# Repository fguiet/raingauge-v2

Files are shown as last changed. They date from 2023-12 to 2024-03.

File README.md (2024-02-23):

# Raingauge v2

## The final project

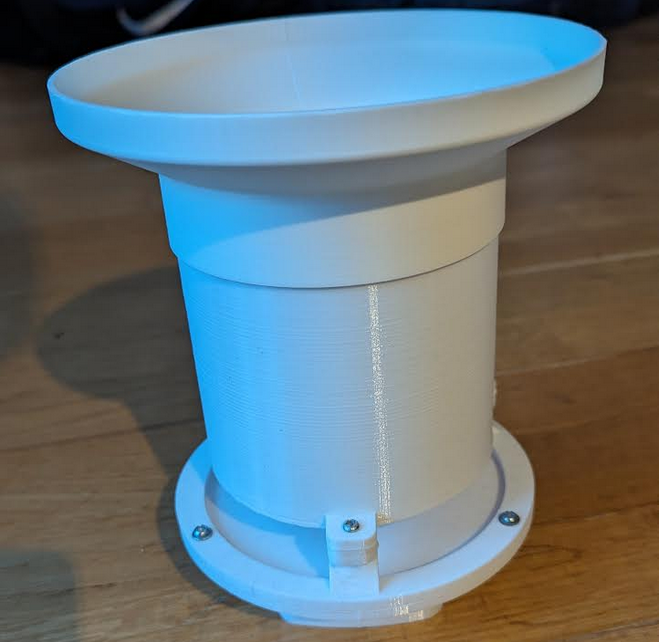
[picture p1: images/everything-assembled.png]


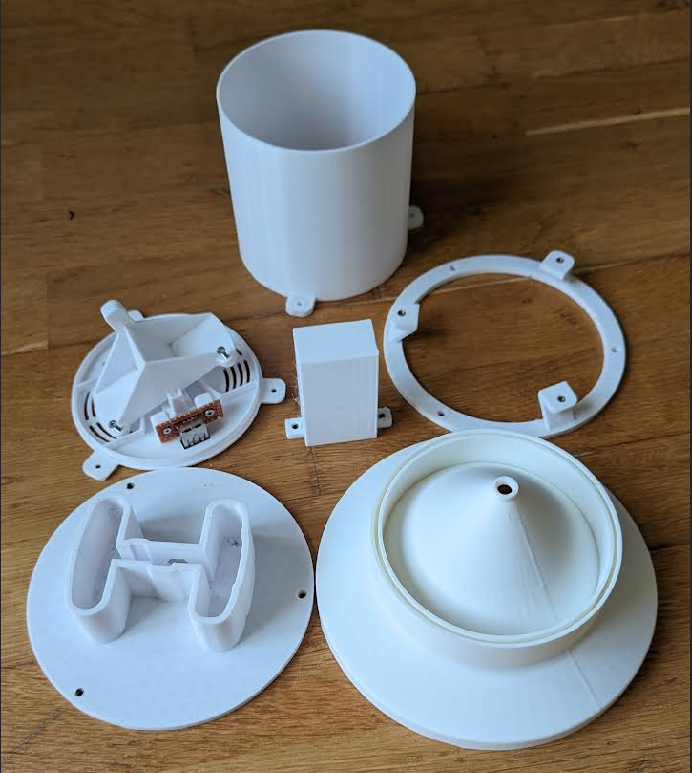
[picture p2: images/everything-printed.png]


This project is available on Thingiverse : <https://www.thingiverse.com/thing:6480016>

## PCB representation

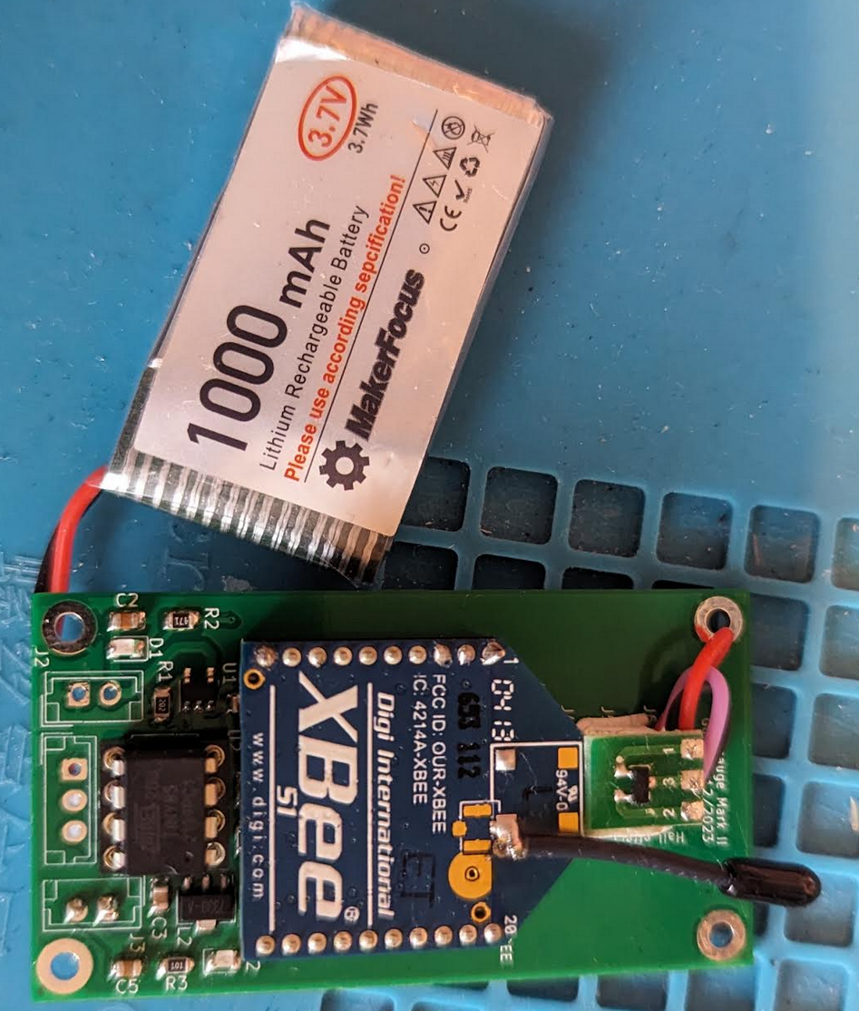
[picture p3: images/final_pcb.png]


## 3D representation

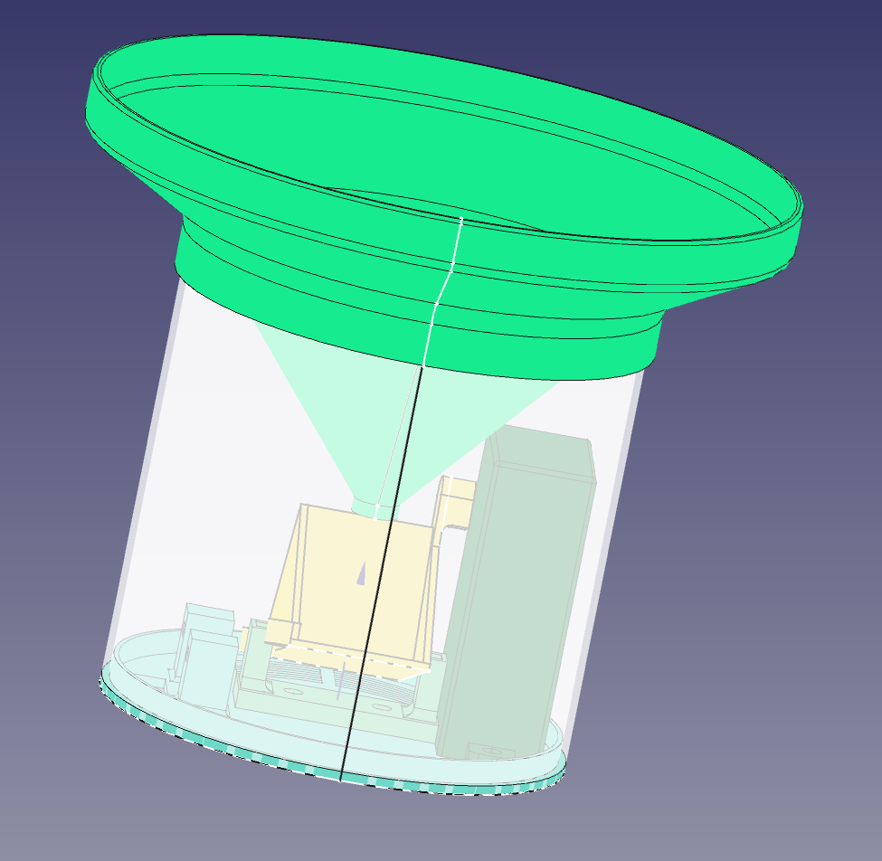
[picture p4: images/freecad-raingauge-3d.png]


## Compute how much water has fell ?

Funnel diameter = 15cm = 150 mm = 0.15m
Volume of each bucket (around) = 3ml = 0.0030l

Funnel area = pi*R² = 3.14 * 0.075² = 0,017669025 m2

X= 1/Aire * V = (1/0,017669025) * 0.0030 = 0.17 L par m2 (ou mm)

1mm = Une litre d'eau tombé sur une mètre carré

Résolution de mon pluvio = 0.17 L/m2 (c'est dans la norme)

## Programming the ATtiny85

Here is the ATtiny 85 pinout

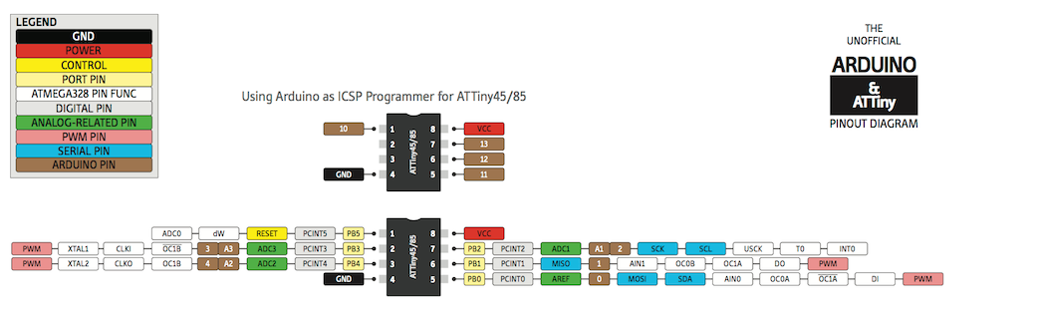
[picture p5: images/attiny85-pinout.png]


Using Arduino IDE v2, use this tutorial : <https://www.instructables.com/How-to-Program-an-Attiny85-From-an-Arduino-Uno/>

1. Use this following URL to add ATtiny Board to Arduino IE <https://raw.githubusercontent.com/damellis/attiny/ide-1.6.x-boards-manager/package_damellis_attiny_index.json>. File => Preferences => Aditional Board URL
2. Install the ATtiny boards (Board Manager on the menu on the left, then Install)
3. __Burn the ArduinoISP Exemple in the Arduino Board (select Arduino Board)__ => Don't forget that ! and make sure ATTiny pin are well connected to the bread board
4. Select ATtiny 85 board
5. Select Clock Internal 1 Mhz (it is ok for this project)
6. Select Programmer => Arduino as ISP
7. Burn Boatloader
8. Open sketch to upload then click on the menu Sketch => Upload using programmer

A quick overview of the Arduino and ATtiny 85 connexion.

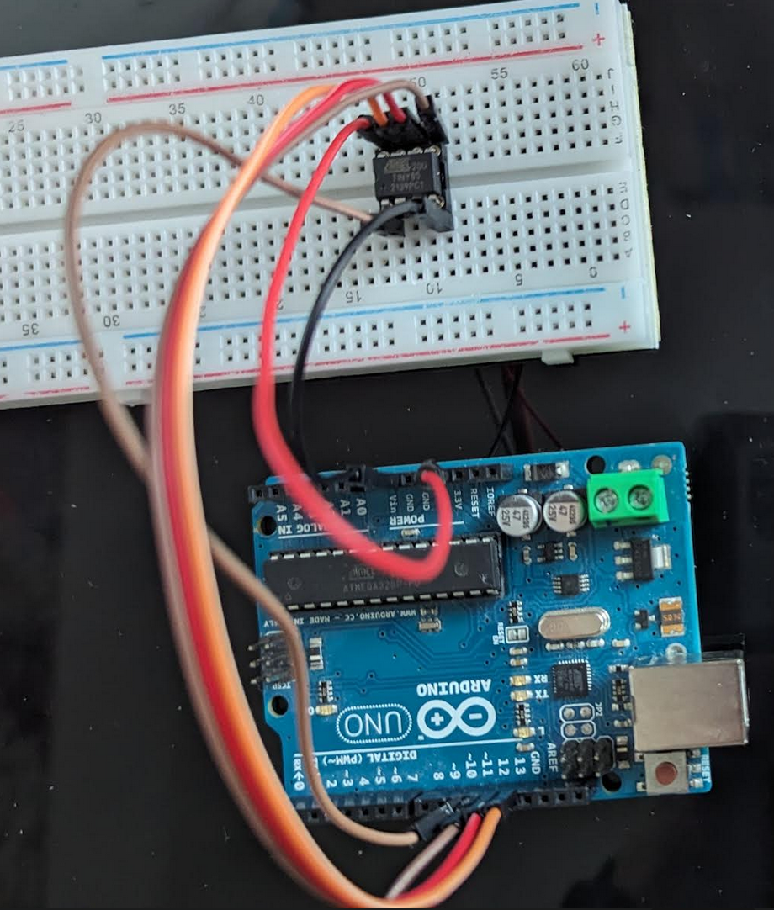
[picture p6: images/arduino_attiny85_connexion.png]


__To program (Arduino <=> ATtiny 85):__

VCC (3.3v ou 5V) <=> VCC (ATtiny pin8)
Arduino GND <=> GND (ATtiny pin4)
Arduino Pin 10 <=> ATtiny Pin1
Arduino Pin 11 <=> ATtiny Pin5
Arduino Pin 12 <=> ATTiny Pin6
Arduino Pin 13 <=> ATTiny Pin7

## Interrupt and power saving stuff with ATtiny 85

See <https://forum.arduino.cc/t/attiny84-sleep-issues/199824/8>
See <http://www.gammon.com.au/power>
See <https://www.marcelpost.com/wiki/index.php/ATtiny84_ADC>

Extract from ATtiny datasheet p49.

²> 9.2 External Interrupts
> Note that recognition of falling or rising edge interrupts on INT0 requires the presence of an
> I/O clock, as described in “Clock Sources” on page 25.

## How to debug using Serial Adapter 

Careful use 3.3v on your serial adapter.

Connect this way:

USB To Serial Adapter <-> ATTiny
GND <-> GND
RX <-> Pin 7 (PB2) 

Then, power the circuit by an external alimentation at 3.3v (no need to power the USB Serial Adapter to VCC pin)

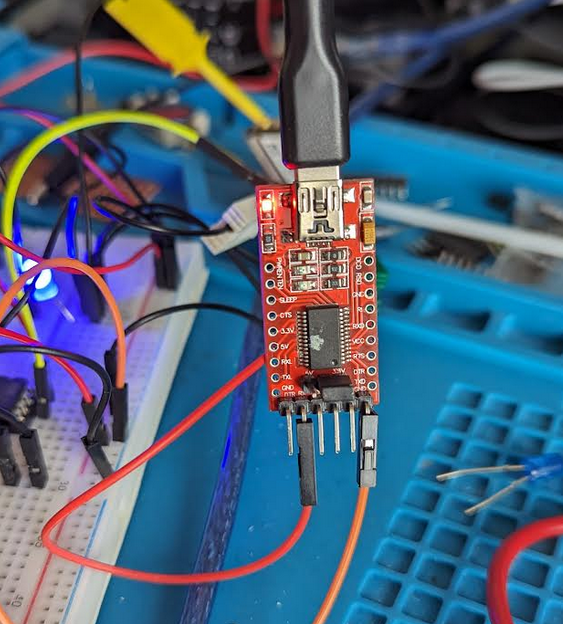
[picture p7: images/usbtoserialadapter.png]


## Power consumption

Using the PPK II (Nordic Power Profiler Kit II), the device consume about 13uA when sleeping and 60mA when sending data.

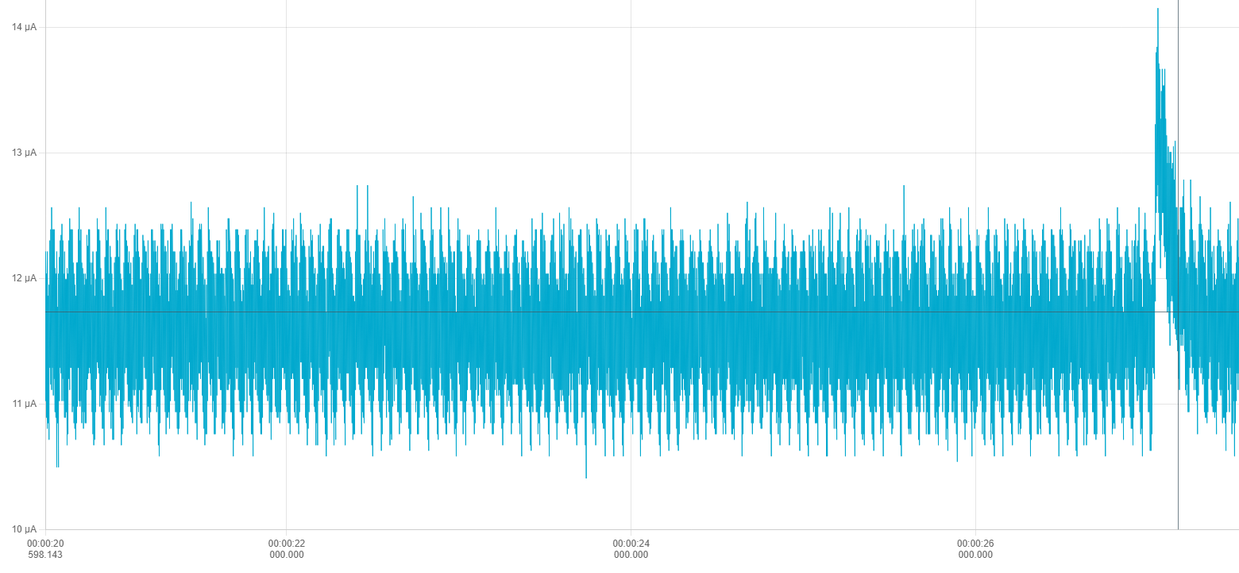
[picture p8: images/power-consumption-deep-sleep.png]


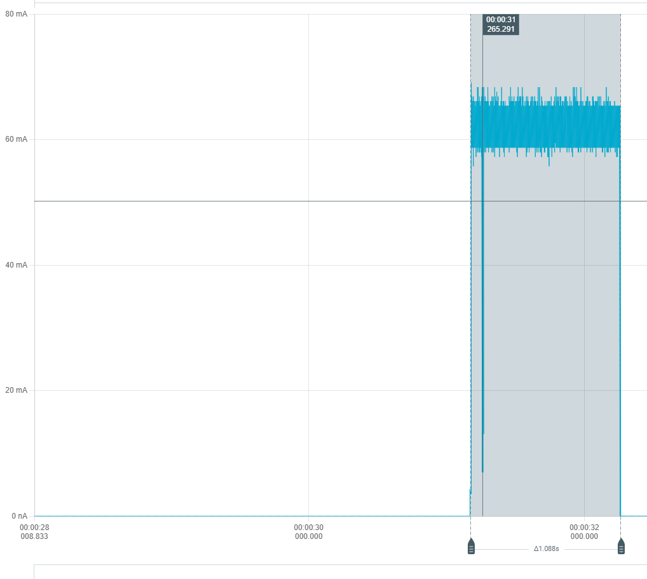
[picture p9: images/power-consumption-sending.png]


VOUT of the PPK II should be connected to VIN of the device and GND to GND.

See [Get your Power Profiler Kit II up and running](https://www.youtube.com/watch?v=B42lPvkUSoc)

## Configuring XBee S1 with XCTU v6.5.13

I am using old XBee S1.

At the begining of the project I was using the transparent mode (AT).

But I changed to API Mode as it offers more options (like the RSSI)

### XBee firmware update

Update the XBee firmware with last version using XCTU v6.5.13

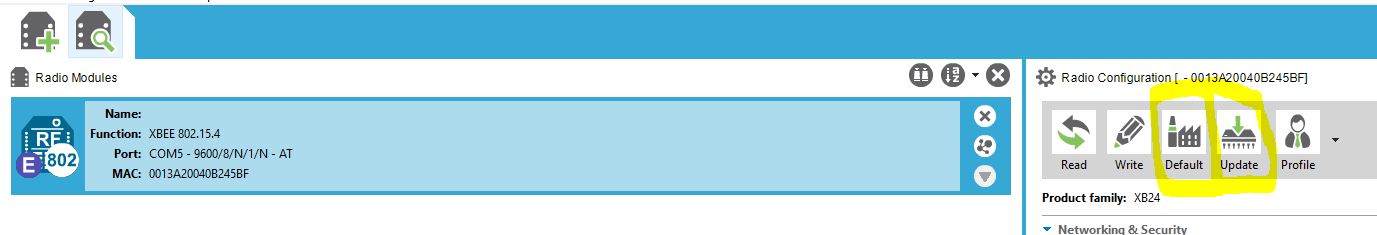
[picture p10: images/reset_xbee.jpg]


Click on Default (To reset XBee to factory default), then Write
Click on Update to upload the last firmware available for this XBee S1 unit

In my case as of 2023/12 :



To make the Xbee talks to each other just config them with the same Channel and PAN (Personnal Area Network ID). Messages will be broadcasted.



### Test XBee communication (deprecated as it shows transparent mode)

You can use XCTU to test that a mesage is correcly sent.

In my case I have got an Raspberry Pi with NodeRed installed and an XBeee connected to the Raspberry Pi.

Just use the XCTU Console and send a test packet, here : "Rainguage projet rocks!" in a JSON format

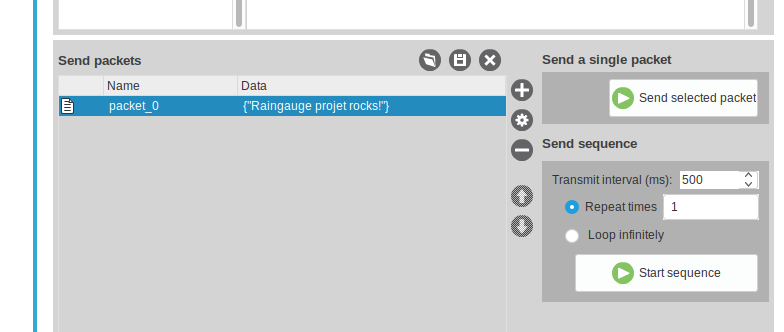
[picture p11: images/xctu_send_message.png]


Here a part of the NodeRed flow I am using.

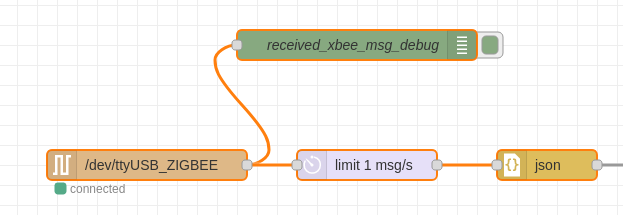
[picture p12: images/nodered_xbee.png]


Careful, you must configure the NodeRed serial flow to split a message as soon as the '}' character is reveiced (end of JSON message)

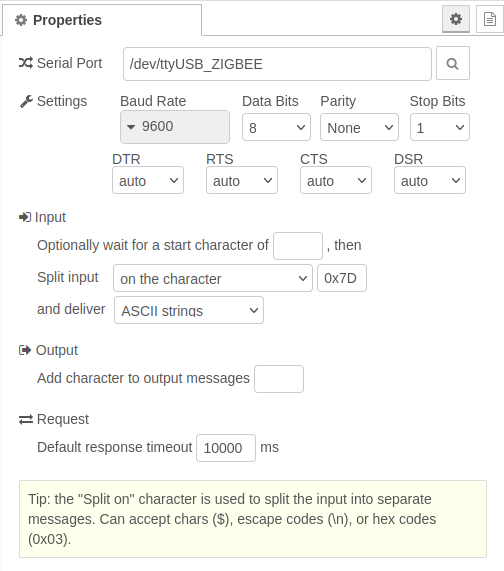
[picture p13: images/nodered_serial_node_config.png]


If everything is going well then you should received the message on the NodeRed debug console

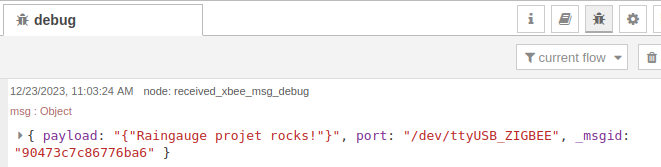
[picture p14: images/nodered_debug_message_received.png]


### XBee pinout

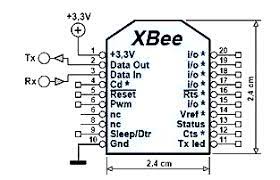
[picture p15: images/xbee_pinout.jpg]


### Sleep mode

To config the Xee to use the sleep mode, just change the sleep mode setting



Sleep mode will be control by pin 9, see <https://www.digi.com/resources/documentation/Digidocs/90001456-13/reference/r_wk_sleep_mode.htm>

PIN 9 HIGH : Xbee sleeps
PIN 9 DOWN : Xbee awake

### XBee speed communication

Don't forget to set Xbee serial speed communication to 38400 bauds as the ATtinySerialOut library use this speed.

### New way of communicating : Using the API Mode

I was using Transparent Mode before (AT) but there is another mode called API Mode that offers more options and controls

See [API mode in detail](https://www.digi.com/resources/documentation/Digidocs/90001942-13/concepts/c_api_mode_detailed.htm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)

See [API Mode 2 frame Structure](https://www.digi.com/resources/documentation/Digidocs/90001942-13/concepts/c_api_frame_structure.htm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)C

Supported frames are listed here : <https://www.digi.com/resources/documentation/Digidocs/90001942-13/reference/r_supported_frames_zigbee.htm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>

I am using the 64-bit Transmit Request - 0x00 frame. I know that I should use the 0x10 frame tpye but I am using old XBee S1 and they only support 802.15.4 protocol stack.

See [64-bit Transmit Request - 0x00](https://www.digi.com/resources/documentation/Digidocs/90001477/reference/r_frame_0x00.htm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)

In API Mode 2, some characters need to be escaped:

See : <https://stackoverflow.com/questions/55861574/difference-between-api-1-and-api-2-mode-of-xbee>

* 0x7E (Start of frame) => 0x7D 0x5E (escaped)
* 0x7D (start of escape sequence) => 0x7D 0x5D (escaped)
* 0x13 (XOFF) => 0x7D 0x33 (escaped)
* 0x11 (XON) =>	0x7D 0x31 (escaped)

In API 2 mode, the length field does not include any escape character in the frame and the checksum is calculated with non-escaped data.

All bytes except for the start delimiter must be escaped if needed.

* End Device XBee configuration

Here is what I changed in the XBee configuration with XCTU

CH - Channel = C
ID - PAN ID = 666
SM - Sleep mode = Pin Hibernate [1]
BD - Interface Data Rate = 38400 [5]
AP - API Enable = API Enabled w/PPP [2]

* Coordinator XBee configuration

CH - Channel = C
ID - PAN ID = 666
CE - Coordinator Enable = Coordinator [1]
BD - Interface Data Rate = 38400 [5]
AP - API Enable = API Enabled w/PPP [2]
RR - XBee Retries = 3 (because the RSSI was not good I tried this setting)

## Librairies used in this project

* ATTinySerialOut

To communicate with the XBee (send data), this project used the following library : `ATtinySerialOut`, version 2.2.0 (2023/12)

GitHub : <https://github.com/ArminJo/ATtinySerialOut/>

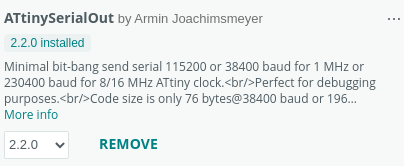
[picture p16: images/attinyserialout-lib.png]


* LowPower

This project is using this library <https://github.com/ortegafernando/Low-Power> to allow the ATTiny 85 power management

__Note__

To use an external library for a Arduino IDE Project, just copy the library source in the librairies folder of Arduino IDE

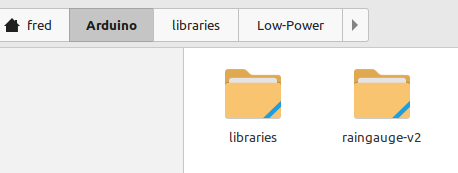
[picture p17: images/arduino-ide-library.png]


## Freecad

__Some notes__

* On ne peut pas utiliser le mirroring sur la pièce que l'on veut "mirrorer" n'a pas de lien avec un objet du body en cours (pas de corps multiples dans un body)

* Utilisation de ShapeBinder pour pouvoir avoir des points de repères d'un autre body (voir vidéo : <https://www.youtube.com/watch?v=KYD9Ojugi8Q>)

### Support tipping bucket

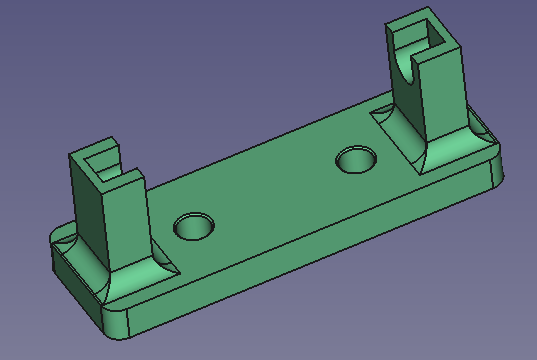
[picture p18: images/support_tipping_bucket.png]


Les trous pour placer les inserts font 4.2mm sur Freecad. les inserts à utiliser sont des M3*4 (4 mm de haut pour type vis M3)

## Pull up / pull down

Quick reminder about pullup/pulldown : <https://arduino.developpez.com/cahiers-pratiques/resistance-pullup-pulldown/>

## Kicad

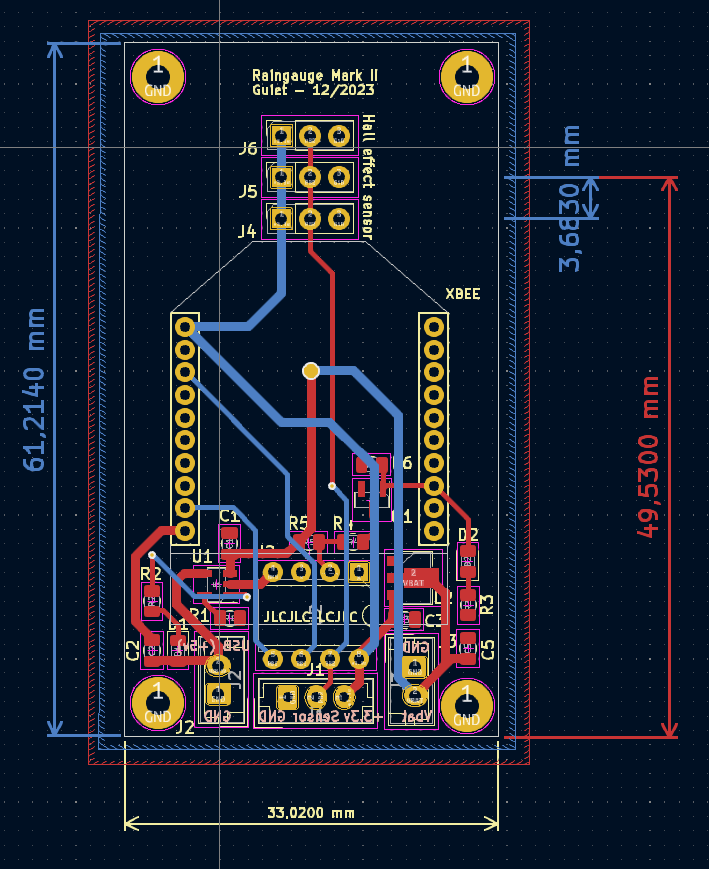
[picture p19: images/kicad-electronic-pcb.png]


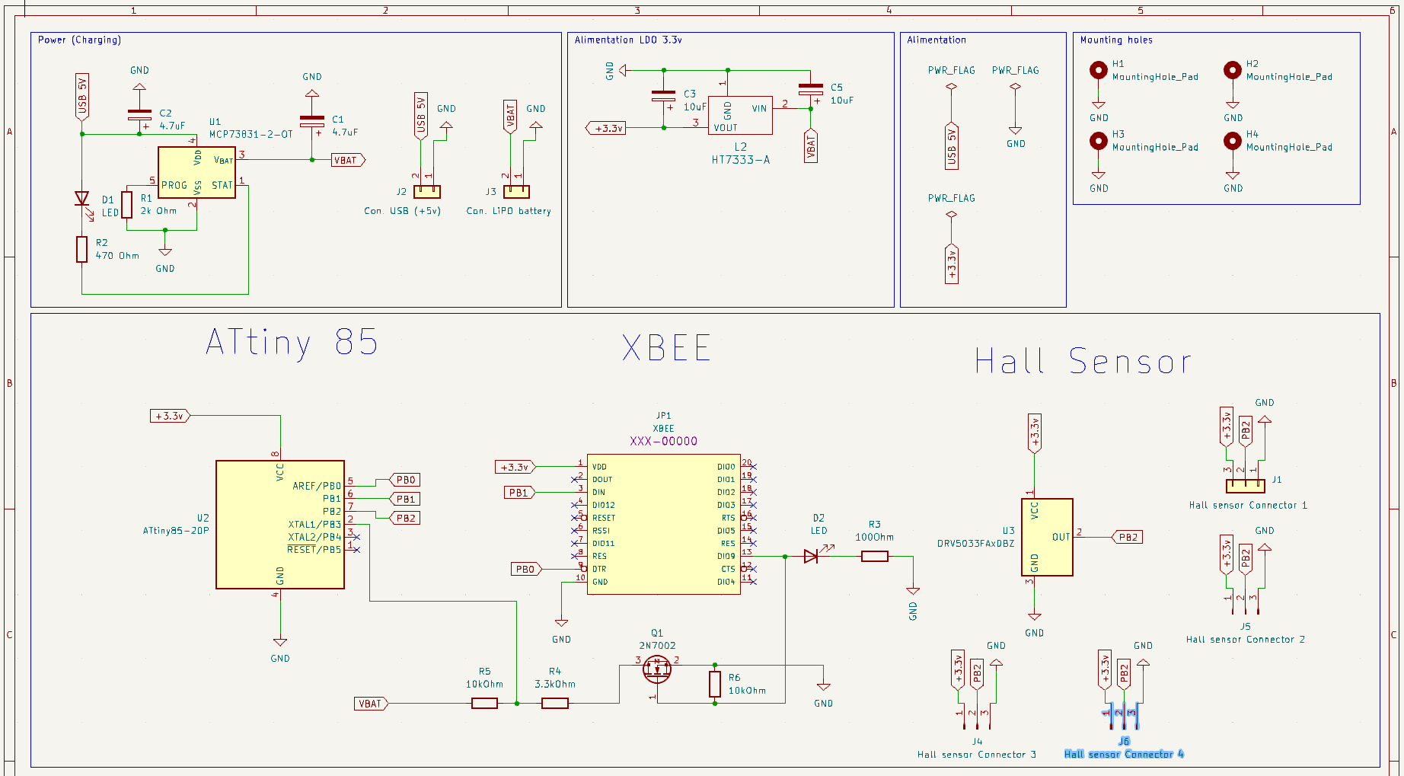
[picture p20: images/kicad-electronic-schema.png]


Ce tuto : <https://www.youtube.com/watch?v=RpVIrzEUsIM> ou <https://www.youtube.com/watch?v=dAck3bxzehA> ou <https://www.youtube.com/watch?v=nYybg5KdaT8>

__Note__ :

Suppression du snap sur le PCB Editor afin de placer les composants à un endroits précis : utiliser la touche CTRL

__Grandes étapes__

1. Editeur de schéma électronique, remplir le cartouche pour définir les informations du PCB

Fichier, Ajustage page

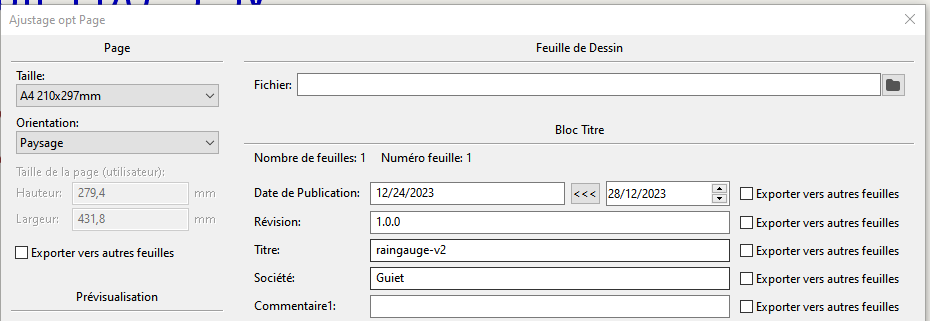
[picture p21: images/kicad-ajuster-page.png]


2. Place all your components

Shortcut

M : Move
R : Rotate
Tab  : Pour bouger le composant avec les fils accrochés

Pour vérifier que le circuit est ok on peut cliquer sur le bouton : 



__Note__

* Essayer de mettre par convention VCC en haut et GND en bas au niveau du positionnement
* Il existe des labels global et local (A voir sur le net la différence)
* Possibilité de créer des feuilles hiérarchiques (si jamais on a un schéma très grand alors on peut le splitter, après y'a les notions de labels hiérarchiques, global, etc etc...)
* Il faut bien penser à définir les pins qui alimentent le schéma électrique (= PWR_FLAG)

3. Annotation de la schématique (pour numéroter les composants)

Normalement avec Kicad 7, les éléments sont numérotés automatiquement.
Sinon, cliquer sur le bouton: 



4. Assigner les empreintes des composants de la schématique



5. Génération de la net liste

Inutile dans Kicad 7 ?

6. Editeur de circuit imprimé et lecture de la net liste

Inutile dans Kicad 7 ?

7. Placement des composants sur l'éditeur de PBB

On passe sur cet écran en cliquant sur :



Récupération des contraintes JLCPCB : <https://github.com/sethhillbrand/kicad_templates/tree/master/JLCPCB_1-2Layer> prendre le fichier JLCPCB.pro

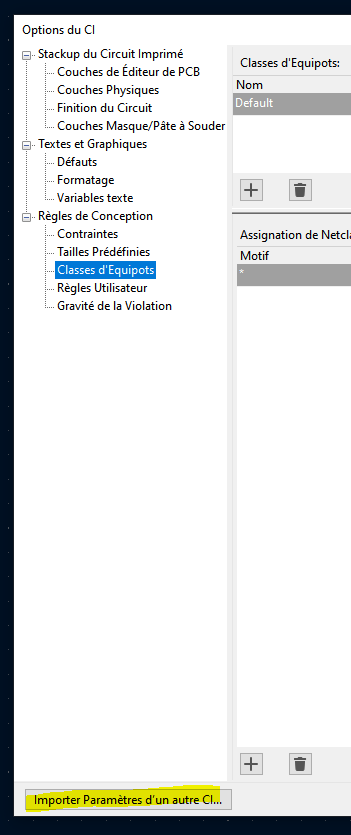
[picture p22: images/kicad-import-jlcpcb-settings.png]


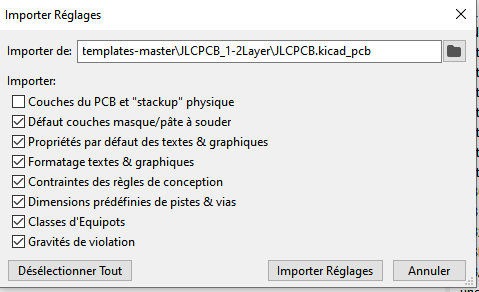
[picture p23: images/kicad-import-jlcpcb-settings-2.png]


Fichier, Ajustage page pour personnaliser le cartouche comme pour l'éditeur de schéma électronique

Pour gérer la largeur des pistes en fonction du type de piste (VCC) : Fichiers, Options CI, Classe d'Equipots, j'utilise 0.4mm pour les pistes classiques et 0.8mm en VCC

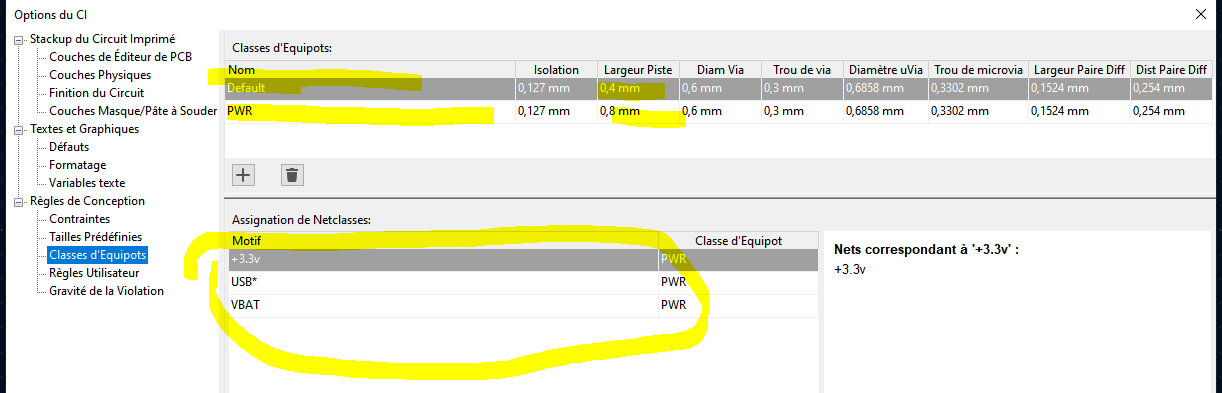
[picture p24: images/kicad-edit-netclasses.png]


Penser à modifier la valeur par défault de la largeur des pistes à 0.4mm

Short Cut

v: change layer (front / bottom)

__Notes__

Layers intéressantes 

F. Silks pour écrire sur le front Silk Screen
B. Silks pour écrire sur le bottom Silk Screen
Dwgs.User pour faire des dessins
F. Courtyard : place que prend le composant front
B. Courtyard : place que prend le composant bottom (on peut afficher ou pas)

Quand il y a beaucoup d'éléments sur le PCB, on peut utiliser le filtre de sélection afin de limiter la sélection à l'objet que l'on désire (exemple j'avais besoin de bouger les références des composants sur la layer silkscreen)

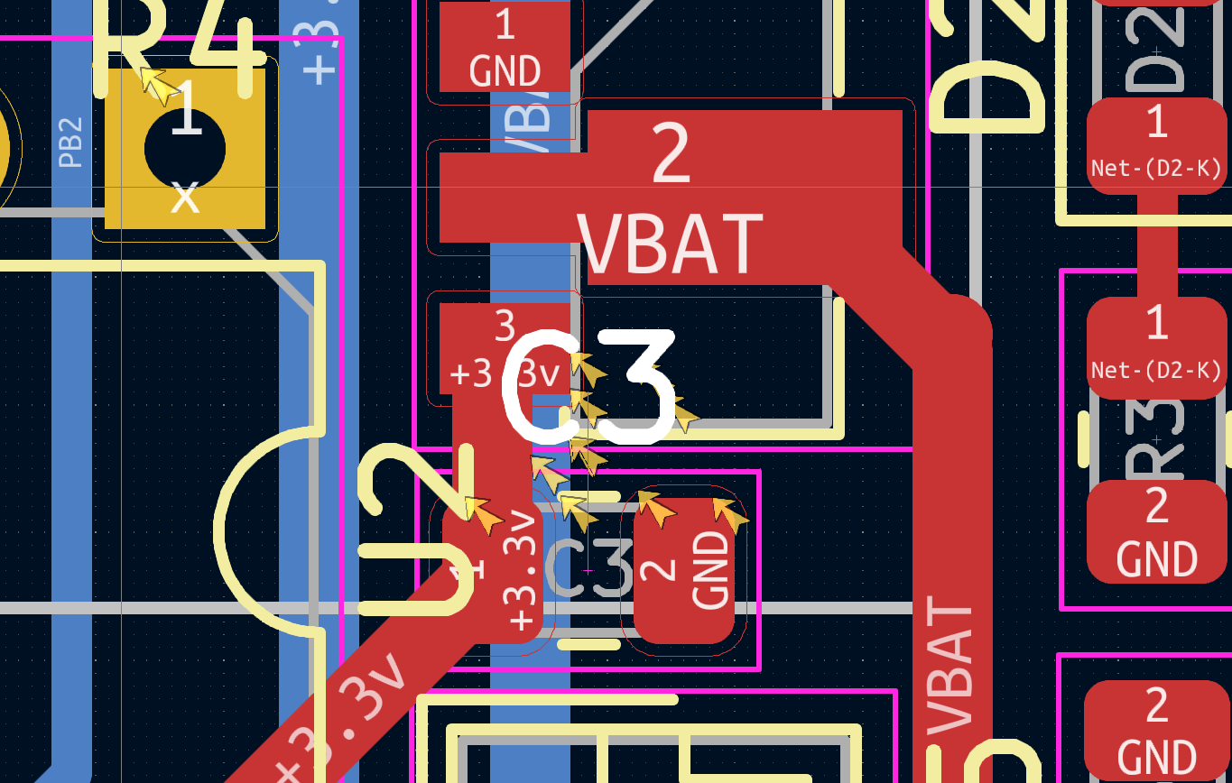
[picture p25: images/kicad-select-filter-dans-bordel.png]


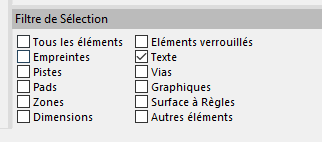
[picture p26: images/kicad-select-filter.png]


8. Couche Edge cut (contour de carte)

On trace autour des composants pour couper le PCB à la taille désirée

9. Routage

Pour la largeur, bien penser à sélectionner utiliser largeur de netclasse.
Attention, dans netclasse il faut avoir penser à modifier la valeur par défaut pour la largeur des pistes à 0.4mm et mettre 0.8mm pour les pistes de puissance (PWR)



Voici ce qu'il faut respecter lors que l'on trace des routages pour éviter les pbs d'électromagnétisme.

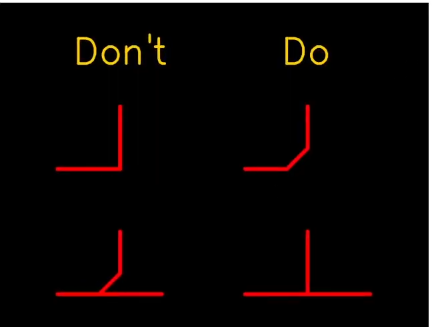
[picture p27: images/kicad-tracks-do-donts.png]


Quand on a des tracks qui se croisent sur la couche du dessus et dessous il faut qu'elles soient perpendiculaires:

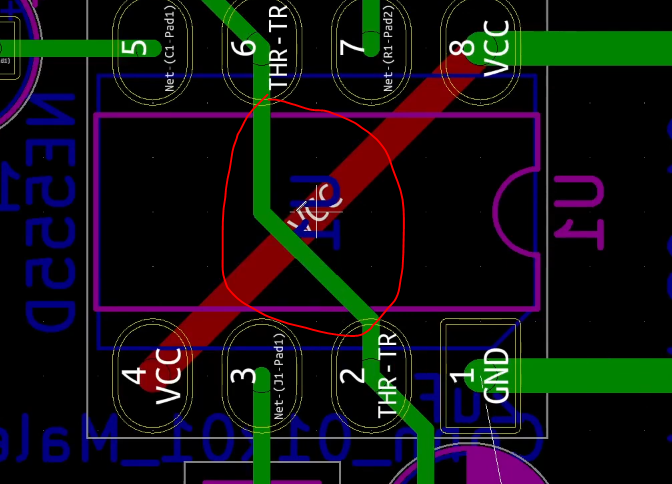
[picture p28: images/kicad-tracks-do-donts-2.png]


Couche F. Cu (Front en rouge couche du dessus)
Couche B. Cu (Front en vert couche du dessous)

Ne pas relier les GND, ca sera automatique avec le plan de masse

__Notes__

Short cut

D : Pour modifer les tracks sans tous casser
I : Au dessus d'une track permet de sélectionner toute la track

10. Ajouter la zone ground (sur layer front / bottom)

Utiliser l'outil : 



10. Serigrafie avec couche Drawing User pour mettre les indications + - et autres ou layer F. Silks et B. Silks

11. Générer les fichiers Gerber, Fichier Tracer (ne pas oublier de générer le fichier de percage)

Mettre un texte JLCJLCJLCJLC sous un composant (layersilk screen)

D'abord générer le fichier de percage (generate drill file) et ensuite plot avec les options par défaut.

12. Faire un Zip et envoyer sur JLCPCB par exemple

## References

* snapeda pour récupérer des composants kicad : <https://www.snapeda.com/>

* Madman's Github : <https://github.com/PricelessToolkit/MailBoxGuard>

* ATTiny and LoRa : <https://github.com/novag/LoRa-ATtiny-Node>

* MrDIY : <https://gitlab.com/MrDIYca/ultra-low-power-trigger-sensors-version-3>

* [MakerMeik : ESP8266 as Window Sensor with years of battery life](https://www.youtube.com/watch?v=vxbuO1zWo3w)

* [ESP32-C3 based Smart Door/Window sensor | DEEP SLEEP 30nA? | Long battery life 5/10 years](https://www.youtube.com/watch?v=he_Z-mDLnlM)

* [Raingauge version 1](https://www.youtube.com/watch?v=DnNW4rJkFhY&t=649s)

* [Raingauge version 2](https://www.youtube.com/watch?v=P2-hs2m6eCE)

* [Communication XBee](https://www.redohm.fr/2015/03/communication-xbee/)

* [Configuration XBee](https://www.electro-info.ovh/configuration-d-un-module-XBEE-avec-XCTU)

* [Un programme qui ressemble a ce que je fais](https://github.com/cano64/ATTiny85-ATTiny84-BMP085-Arduino-Library-FastAltitude/issues/1)

* [How works a switch without neutral](https://www.youtube.com/watch?v=VNYcD7MEp4A)

* [Inspiring sketch : OpenWindowAlarm](https://github.com/ArminJo/ATtinySerialOut/blob/master/examples/OpenWindowAlarm/OpenWindowAlarm.ino)

* [OpenWindowAlarm documentation](https://github.com/ArminJo/Arduino-OpenWindowAlarm)

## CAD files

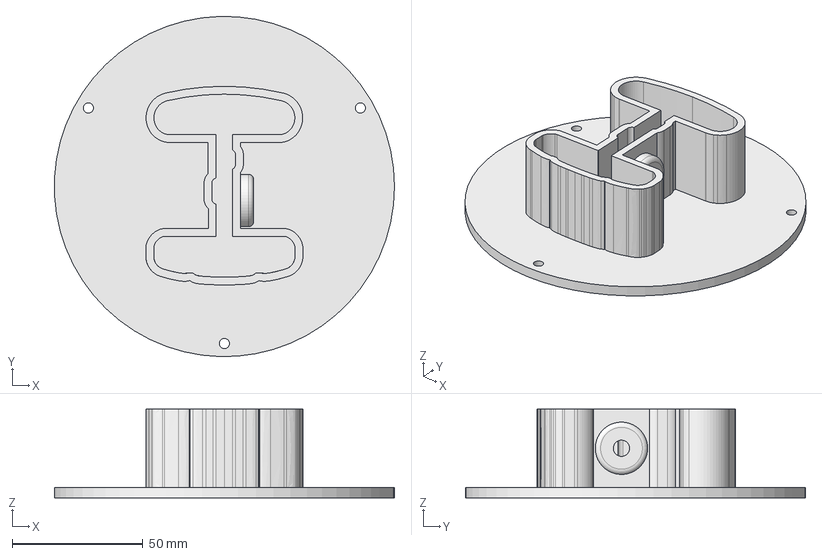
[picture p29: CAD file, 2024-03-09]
freecad/raingauge-pole-support.FCStd
129.9 x 130.0 x 34.0 mm

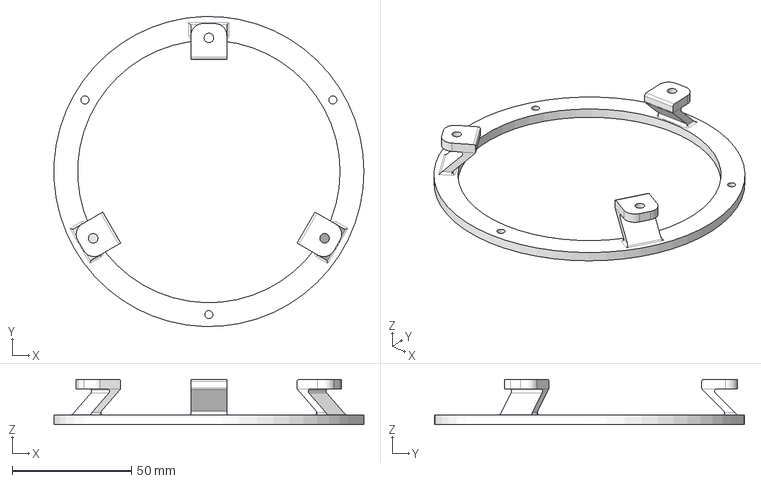
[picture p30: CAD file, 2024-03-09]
freecad/rainguage-final.FCStd
129.9 x 129.9 x 19.0 mm

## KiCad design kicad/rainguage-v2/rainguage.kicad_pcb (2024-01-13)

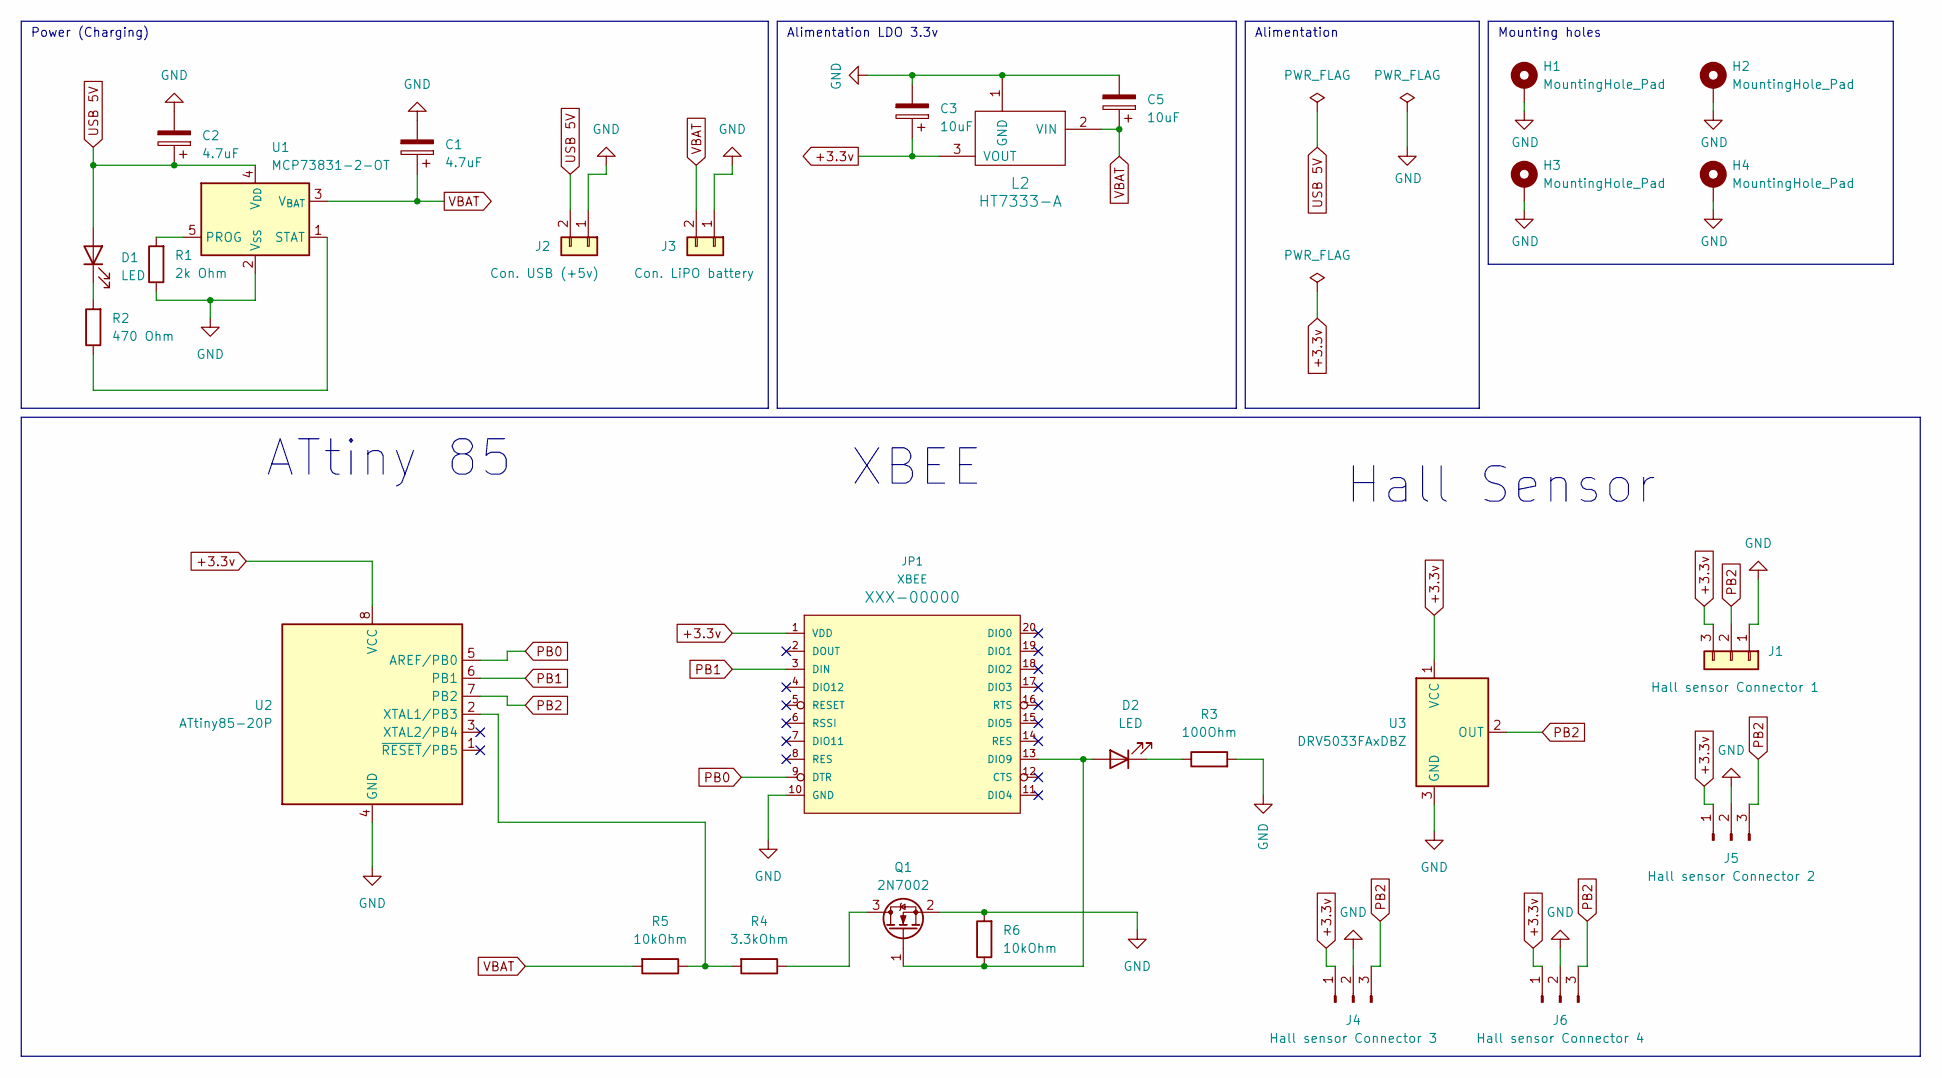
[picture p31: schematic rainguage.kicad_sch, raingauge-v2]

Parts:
C1, C2: 4.7uF; C_0805_2012Metric
C3, C5: 10uF; C_0805_2012Metric
D1, D2: LED; LED_0805_2012Metric
H1, H2, H3, H4: MountingHole_Pad; MountingHole_2.2mm_M2_Pad
J1: Hall sensor Connector 1; JST_EH_B3B-EH-A_1x03_P2.50mm_Vertical
J2: Con. USB (+5v); JST_EH_B2B-EH-A_1x02_P2.50mm_Vertical
J3: Con. LiPO battery; JST_EH_B2B-EH-A_1x02_P2.50mm_Vertical
J4: Hall sensor Connector 3; PinSocket_1x03_P2.54mm_Vertical
J5: Hall sensor Connector 2; PinSocket_1x03_P2.54mm_Vertical
J6: Hall sensor Connector 4; PinSocket_1x03_P2.54mm_Vertical
JP1: XBEE
L2: HT7333-A; SOT-89-3
Q1: 2N7002; SOT-23
R1: 2k Ohm; R_0805_2012Metric
R2: 470 Ohm; R_0805_2012Metric
R3: 100Ohm; R_0805_2012Metric
R4: 3.3kOhm; R_0805_2012Metric
R5, R6: 10kOhm; R_0805_2012Metric
U1: MCP73831-2-OT; SOT-23-5
U2: ATtiny85-20P; DIP-8_W7.62mm
U3: DRV5033FAxDBZ; SOT-23

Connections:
+3.3v: C3.1, J1.3, J4.1, J5.1, J6.1, JP1.1 (VDD), L2.3 (VOUT), U2.8 (VCC), U3.1 (VCC)
GND: C1.2, C2.2, C3.2, C5.2, H1.1, H2.1, H3.1, H4.1, J1.1, J2.1, J3.1, J4.2, J5.2, J6.2, JP1.10 (GND), L2.1 (GND), Q1.2 (S), R1.1, R3.2, R6.2, U1.2 (V_{SS}), U2.4 (GND), U3.3 (GND)
unnamed: D1.1 (K), R2.2
unnamed: D2.2 (A), JP1.13 (DIO9), Q1.1 (G), R6.1
unnamed: D2.1 (K), R3.1
unnamed: Q1.3 (D), R4.1
unnamed: R1.2, U1.5 (PROG)
unnamed: R2.1, U1.1 (STAT)
unnamed: R4.2, R5.1, U2.2 (XTAL1/PB3)
PB0: JP1.9 (DTR), U2.5 (AREF/PB0)
PB1: JP1.3 (DIN), U2.6 (PB1)
PB2: J1.2, J4.3, J5.3, J6.3, U2.7 (PB2), U3.2 (OUT)
USB 5V: C2.1, D1.2 (A), J2.2, U1.4 (V_{DD})
VBAT: C1.1, C5.1, J3.2, L2.2 (VIN), R5.2, U1.3 (V_{BAT})

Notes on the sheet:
XBEE
Power (Charging)
Hall Sensor
Mounting holes
Alimentation
Alimentation LDO 3.3v
ATtiny 85

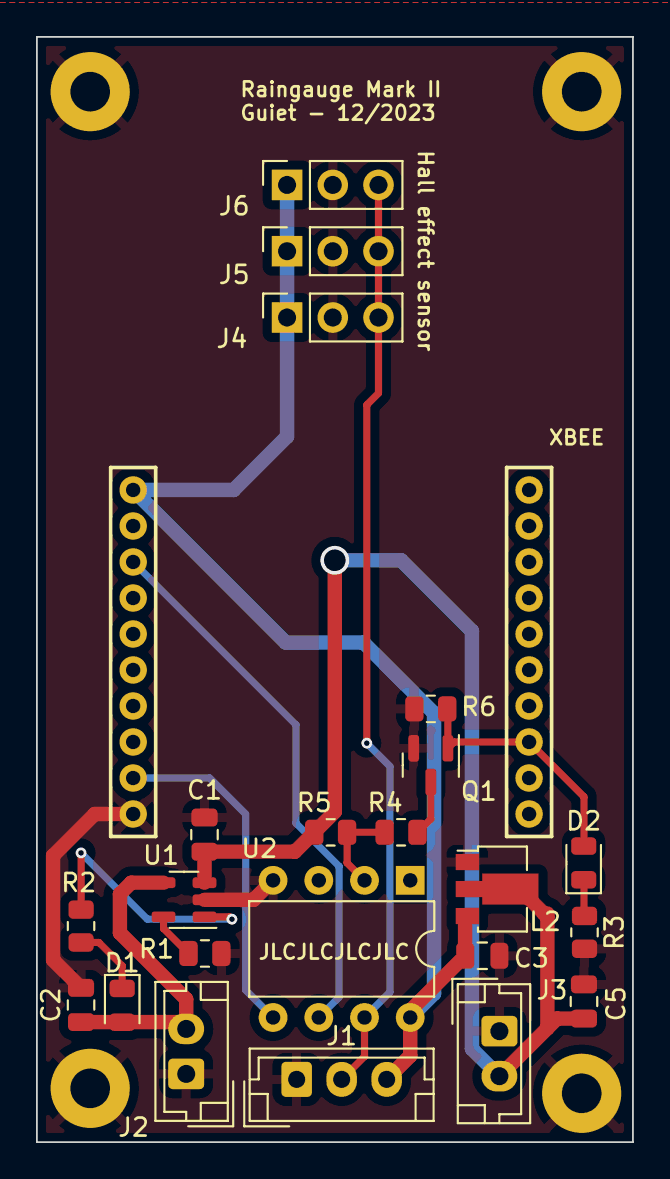
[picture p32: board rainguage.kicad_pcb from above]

Board: 2 copper layers, 33.1 x 61.4 mm, 27 parts (0 on the bottom side), 14 nets.

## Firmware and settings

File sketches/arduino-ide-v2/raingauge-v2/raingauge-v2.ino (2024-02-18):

/*
 *  Rainguage-v2 project
 *  
 *  Description:
 *     
 *     This program uses interrupt to detect when a raingauge tipping bucket is tipping.
 *
 *     Detection is done by the help of an Low Power Consumption Hall Effect Sensor : DRV5032FADBZR
 *
 *     Then it wakes up the XBee and send a message
 *
 *     The message is received on another XBee plugged in a Raspberry.
 *
 *     A Nodered flow then received the message and handles so it is consumed by HomeAssistant
 *     
 *     This is an ultra low power battery operated design. It consumes only XXuA when sleeping.
 *     
 *     More info here : https://github.com/fguiet/raingauge-v2
 *     
 *  Board used : Using board 'ATtiny85' 
 *               Using Arduino As ISP to program the ATtiny85
 *     
 *  Date : 2023/12/23
 *  
 *  Version : 1.0
 *  
 */

#include <Arduino.h>  // required for main()

// Note :
//   - See https://github.com/ArminJo/ATtinySerialOut/blob/master/README.md#compile-options--macros-for-this-library
//   - By default the ATtinySerialOut is using the PIN_PB2 (physical Pin 7)
//   - By default The rates are 38400 baud at 1 MHz

//Change default (PINB2) TX Pin to PINB1
#define TX_PIN PINB1

//Uncomment this line below if you want to use 38400 bauds instead of 115200 bauds
#define TINY_SERIAL_DO_NOT_USE_115200BAUD

#include "ATtinySerialOut.hpp"  // Available as Arduino library "ATtinySerialOut"

//From https://github.com/ortegafernando/Low-Power/tree/master
#include "LowPower.h"

unsigned int eightSecondsPassedCounter = 0;

//450 * 8 = 3600 secons
const int ONE_HOUR = 450;
const String SENSOR_ID = "1";
const String FIRMWARE_VERSION = "1.0.0";
const byte ADC_PIN = PINB3;                             //Physical PIN 2
const byte WAKE_XBEE_PIN = PINB0;                       //ie PIN_PB0 - Physical PIN 6
const byte INTERRUPT_NUMBER = 0;                        // This is the interrupt number linked to PB2 (See schematic) - INT0
const byte PHYSICAL_PIN_LINK_TO_INTERRUPT_PIN = PINB2;  //Physical PIN 6 - PIN_PB1 link to PCINT1 (see schematic)
const byte BATTERY_READING = 5;
const uint8_t XBEE_COORDINATOR_ADDRESS[] = {0x00,0x13,0xA2,0x00,0x40,0xB4,0xC3,0x6C};
volatile bool isTippingOccured = false;

//Tip counter
int tip_cpt = 0;
int tip_cpt_rain = 0;

void setup() {
  // Must be called once if pin is not set to output otherwise
  initTXPin();

  //Set Interrupt pin to HIGH
  pinMode(PHYSICAL_PIN_LINK_TO_INTERRUPT_PIN, INPUT_PULLUP);

  //Setting the XBee Sleeping Pin to HIGH = Go to sleep my friend
  pinMode(WAKE_XBEE_PIN, OUTPUT);
  digitalWrite(WAKE_XBEE_PIN, HIGH);
}

void loop() {

  //Reinit variable
  isTippingOccured = false;

  //Reset tip_counter every 32 000 tips
  //This value can be used to control whether all tips are received
  if (tip_cpt==32000) tip_cpt=0;
  if (tip_cpt_rain==32000) tip_cpt_rain=0;
  
  //Attach interrupt
  attachInterrupt(INTERRUPT_NUMBER, fakeFunction, LOW);

  //Using for method is not working...
  //for (unsigned long i= 0; i < ONE_HOUR_SECONDS; i++) {
    LowPower.powerDown(SLEEP_8S, ADC_OFF, BOD_OFF);    
    eightSecondsPassedCounter++;
  //}

  //Detach interrupt
  detachInterrupt(INTERRUPT_NUMBER);

  if (eightSecondsPassedCounter >= ONE_HOUR || isTippingOccured) {

    if (isTippingOccured)
      //Increase tip counter
      tip_cpt_rain++;      
    else
      tip_cpt++;

    advertiseTipOccured();

    //Reset counter
    eightSecondsPassedCounter = 0;
  } 
}

void fakeFunction() {
  isTippingOccured = true;
}

// Needed to compute ZigBee API 2 mode frame length
void computeMSB_LSB(uint16_t number, uint8_t &msb, uint8_t &lsb) {
    msb = (number >> 8) & 0xFF; // Shift right by 8 bits to get MSB
    lsb = number & 0xFF;        // Mask to get LSB
}

// See https://forum.arduino.cc/t/how-to-calculate-checksum-for-16bit-address-xbee-tx-frame/439001/4
uint8_t calculateChecksum(const uint8_t* data, size_t length) {  
  uint8_t checksum = 0;
  for (size_t i = 0; i < length; ++i) {
    //Serial.println(data[i],HEX);
    checksum += data[i];
  }  
  checksum &= 0xFF;        // low order 8 bits
  checksum = 0xFF - checksum; // subtract from 0xFF

  return  checksum;
}

//Create the ZigBee Mode API 2 - frame
//
//Using 0x00 - 64-bit Transmit Request (Deprecated one, should use 0x10 but I am using old XBee S1 (802.15.4 protocol stack)
//See https://www.digi.com/resources/documentation/Digidocs/90001477/reference/r_frame_0x00.htm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
void createAndSendZigBeeAPIFrame(String message) {
  
  //Gets an array of String : message
  byte messageArray[message.length()+1];
  message.getBytes(messageArray, message.length()+1);

  //Get messageArraySize
  int messageArraySize = sizeof(messageArray) / sizeof(messageArray[0]);
  
  //Declare array with needed space for message + need byte of frame
  uint8_t frame[14+sizeof(messageArray)]; 
  
  //Empty frame
  for (int i=0; i < sizeof(frame) / sizeof(frame[0]) -1; i++) {    
    frame[i] = 0;    
  }

  //Initialize Frame
  frame[0] = 0x7E; // Start delimiter
  //
  frame[1] = 0x00; // Length MSB (to be updated later)
  frame[2] = 0x00; // Length LSB (to be updated later)
  //
  frame[3] = 0x00; // Frame type ie 0x00 - Tx (Transmit) - Request: 64-bits address
  // 
  frame[4] = 0x42; // Frame ID 0x42 why not ;-)
  //
  // Desination address : here my coordinator 
  for (int i=0; i <= sizeof(XBEE_COORDINATOR_ADDRESS) -1; i++) {
    frame[5+i] = XBEE_COORDINATOR_ADDRESS[i];
  }

  /*frame[5] = 0x00; 0
  frame[6] = 0x13; 
  frame[7] = 0xA2;
  frame[8] = 0x00;
  frame[9] = 0x40;
  frame[10] = 0xB4;
  frame[11] = 0xC3;
  frame[12] = 0x6C;*/
  
    //
  frame[13] = 0x00; // Options
  //
  // DATA      
  for (int i=0; i < messageArraySize-1; i++) { 
    //Serial.println("TOTO:"+String(messageArray[i], HEX));
    frame[14+i] = messageArray[i];    
  }
  //Checksum = all data except start + length (on non escaped data)
  //Start compute at frame+3 (ie frame type) to 11 (frame type to options + message size)
  frame[14+messageArraySize-1] = calculateChecksum(frame+3, 11+messageArraySize-1);

  //In API 2 mode, the length field does not include any escape character in the frame and the checksum is calculated with non-escaped data.  
  uint8_t msb, lsb;
  //Serial.println("Message Size = " + String(11+messageArraySize-1));
  computeMSB_LSB(11+messageArraySize-1, msb, lsb);  

  //Serial.print("MSB: 0x");
  //Serial.println(msb, HEX);

  //Serial.print("LSB: 0x");
  //Serial.println(lsb, HEX);

  //Set frame length
  frame[1] = msb;
  frame[2] = lsb;

  int j=1;
  //Compute number final arraylenght necessary with escaped characters needed
  for (int i=1; i < 14+messageArraySize; i++) {
    
    if (frame[i] == 0x7E 
     || frame[i] == 0x7D 
     || frame[i] == 0x13
     || frame[i] == 0x11)
      j++;
    
    j++;
  }

  //
  // DEBUG
  //
  /*Serial.println("DEBUT FRAME");
  for (int i=0; i < sizeof(frame); i++) {    
    Serial.print("0x" + String(frame[i], HEX) + " ");
  }
  Serial.println("FIN FRAME");
  return ;*/

  //Escape frame (all byte exept Start delimiter)
  uint8_t escapedFrame[j];

  //Start delimiter
  escapedFrame[0] = frame[0];
  j = 1;

  for (int i=1; i < 14+messageArraySize; i++) {
    
    if (frame[i] == 0x7E) {
      escapedFrame[j] = 0x7D;
      j++;
      escapedFrame[j] = 0x5E;      
      j++;
      continue;
    }

    if (frame[i] == 0x7D) {
      escapedFrame[j] = 0x7D;
      j++;
      escapedFrame[j] = 0x5D;      
      j++;
      continue;
    }

    if (frame[i] == 0x13) {
      escapedFrame[j] = 0x7D;
      j++;
      escapedFrame[j] = 0x33;      
      j++;
      continue;
    }

    if (frame[i] == 0x11) {
      escapedFrame[j] = 0x7D;
      j++;
      escapedFrame[j] = 0x31;      
      j++;
      continue;
    }
    
    //other case
    escapedFrame[j] = frame[i];
    j++;

  }
  //
  // DEBUG
  //
  /*Serial.println("DEBUT FRAME");
  for (int i=0; i < sizeof(escapedFrame); i++) {    
    Serial.print("0x" + String(escapedFrame[i], HEX) + " ");
  }
  Serial.println("FIN FRAME");*/

  //Send frame
  //Serial.write(escapedFrame);
  
  //char tt []= {0x7E, 0x00, 0x7D, 0x33, 0x00, 0x42, 0x00, 0x7D, 0x33, 0xA2, 0x00, 0x40, 0xB2, 0x45, 0xBF, 0x00, 0x66, 0x72, 0x65, 0x64, 0x65, 0x72, 0x69, 0x63, 0xCE};

  //WORKING
  //char tt [] = {0x7e, 0x0, 0x2a, 0x0, 0x42, 0x0, 0x7d, 0x33, 0xa2, 0x0, 0x40, 0xb2, 0x45, 0xbf, 0x0, 0x7b, 0x22, 0x74, 0x69, 0x70, 0x22, 0x3a, 0x22, 0x74, 0x72, 0x75, 0x65, 0x22, 0x2c, 0x22, 0x62, 0x61, 0x74, 0x74, 0x65, 0x72, 0x79, 0x22, 0x3a, 0x22, 0x32, 0x2e, 0x34, 0x32, 0x22, 0x7d, 0x5d, 0x9c};
  //for (int i=0;i<sizeof(tt);i++) {
  //  Serial.print(tt[i]);    
  //}
  //uint8_t tt []= {0x7E, 0x00, 0x7D, 0x33, 0x00, 0x42, 0x00, 0x7D, 0x33, 0xA2, 0x00, 0x40, 0xB2, 0x45, 0xBF, 0x00, 0x66, 0x72, 0x65, 0x64, 0x65, 0x72, 0x69, 0x63, 0xCE};
  //char* ptr = escapedFrame;
  //Serial.print(tt);

  for (int i=0;i<sizeof(escapedFrame);i++) {
    Serial.print((char)escapedFrame[i]);    
  }

  //Serial.flush();
}

void advertiseTipOccured() {

  String tippingOccured = "f";

  //Wakeup XBee
  digitalWrite(WAKE_XBEE_PIN, LOW);

  //Wait for XBee to wake up don't be so impatient
  delay(50);

  float battery_voltage = averageVoltage();

  if (isTippingOccured)
    tippingOccured = "t";

  //Send message  
  //String message = "{\"id\":\""+SENSOR_ID+"\",\"fw\":\""+FIRMWARE_VERSION+"\",\"tip\":\""+tippingOccured+"\",\"bat\":\""+ String(battery_voltage,2)+"\",\"cpt_rain\":"+ String(tip_cpt_rain)+",\"cpt\":"+String(tip_cpt)+"}";
  //String message = "frederic";
  String message = "{\"id\":\""+SENSOR_ID+"\",\"fw\":\""+FIRMWARE_VERSION+"\",\"t\":\""+tippingOccured+"\",\"b\":\""+ String(battery_voltage,2)+"\",\"c1\":"+String(tip_cpt)+",\"c2\":"+String(tip_cpt_rain)+"}";

  //Send ZigBee message using API Mode 2 
  createAndSendZigBeeAPIFrame(message);
  
  //Wait for XBee to send the message and avoid to send multiple messages
  delay(1000);

  //Go to sleep XBee
  digitalWrite(WAKE_XBEE_PIN, HIGH);
}

// Compute an average voltage
float averageVoltage() {

  // set the ADC reference to 1.1V
  analogReference(INTERNAL);    
  
  int total = 0;
     
  for(byte i=0;i<BATTERY_READING;i++) {
    total = total + analogRead(ADC_PIN);
  }
     
  int averageSensor = total / BATTERY_READING; 
  
  //ADC reading = 964 for 4.2v
  float voltage = (averageSensor * 4.20) / 964;
  
  return voltage;             
}

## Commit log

2023-12-23 First commit of this fabulous project ;-)
    [rainguage-test-2.FCStd]
2023-12-26 Update doc
    [rainguage-test-2.FCStd, rainguage.kicad_pcb, rainguage.kicad_sch]
2023-12-28 Petit commit des familles
2023-12-28 commit des familles
    [rainguage-test-2.FCStd, rainguage.kicad_pcb, rainguage.kicad_sch]
2023-12-31 add 3d representation
    [rainguage-test-2.FCStd]
2024-01-20 Add arduino ide sketch
2024-03-09 Update freecad design
    [raingauge-pole-support.FCStd, rainguage-final.FCStd]
